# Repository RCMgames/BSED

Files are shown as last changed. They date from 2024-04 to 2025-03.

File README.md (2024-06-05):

# Byte Sized Encoder Decoder






Reads 8 quadrature encoders and communicates over I2C.

https://github.com/RCMgames/BSED

* Reads 8 quadrature encoders
* 1.0x0.85 inches, 25.4x21.59 millimeters
* I2C (Qwiic Compatible)
* powered by an ATmega328PB
* hand solderable surface mount components

### links 
(this repository contains an Arduino library, firmware for the board, and hardware for the board)
* [Documentation for Library](https://rcmgames.github.io/BSED/class_byte_sized_encoder_decoder.html)
* [Hardware](https://github.com/RCMgames/BSED/tree/main/extras/hardware)
  * If you buy PCBs from PCBWay through this link PCBWay generously gives me a 10% commission without costing you anything
    * https://www.pcbway.com/project/shareproject/ByteSizedEncoderDecoder_v1_1_a5a4bd50.html
* [Firmware](https://github.com/RCMgames/BSED/tree/main/extras/firmware)

### testing
Approximately 15000 encoder counts per second can be read from each encoder, but do your own testing before trusting this software.

See, and contribute to, this discussion on testing results: https://github.com/RCMgames/BSED/discussions/6

I've been working on [hardware and software for small wifi controlled robots](https://github.com/rcmgames) since 2020.

As I have designed increasingly small [circuit boards](https://github.com/rcmgames) for controlling servos and motors on robots, I started looking for a way to connect lots of quadrature encoders as inputs to a microcontroller. I was unable to find any existing Qwiic-compatible encoder reading boards that can handle multiple high-speed quadrature inputs. This board can help you control 8 motors with encoder feedback for precise control.

This version of firmware and library are compatible with version 1 of the hardware.

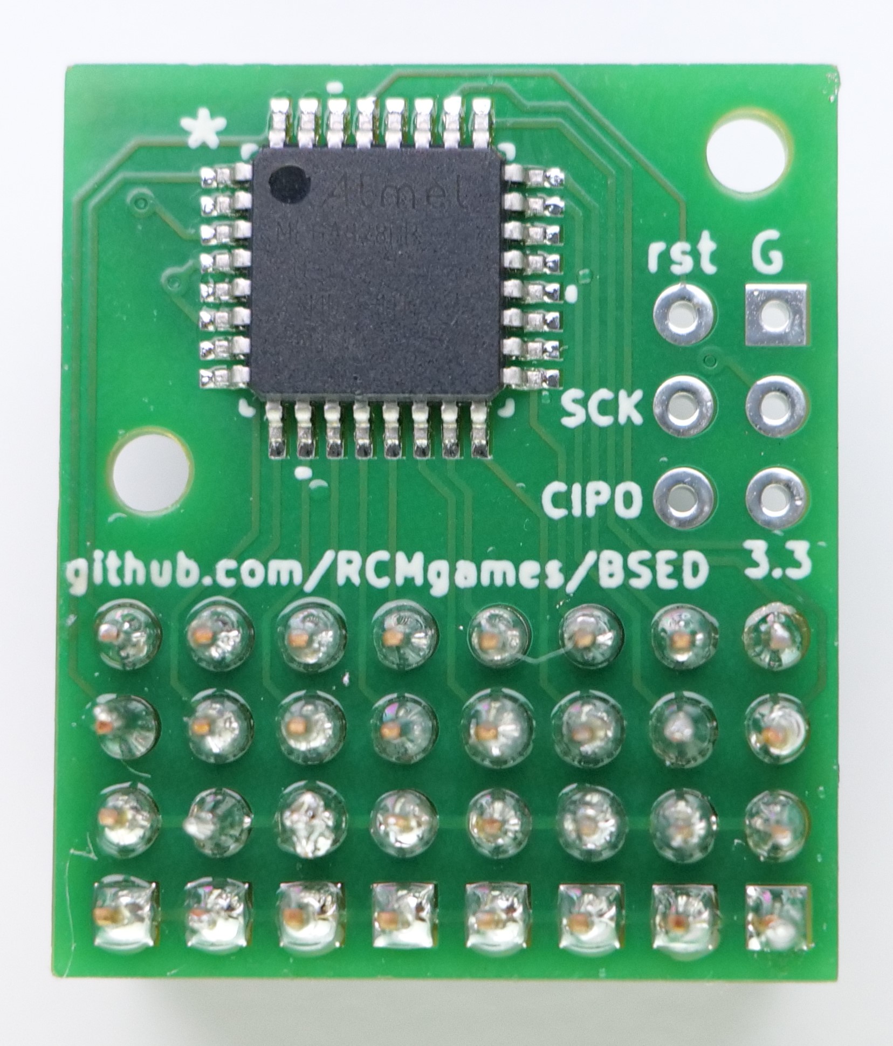
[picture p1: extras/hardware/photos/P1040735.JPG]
back of pcb

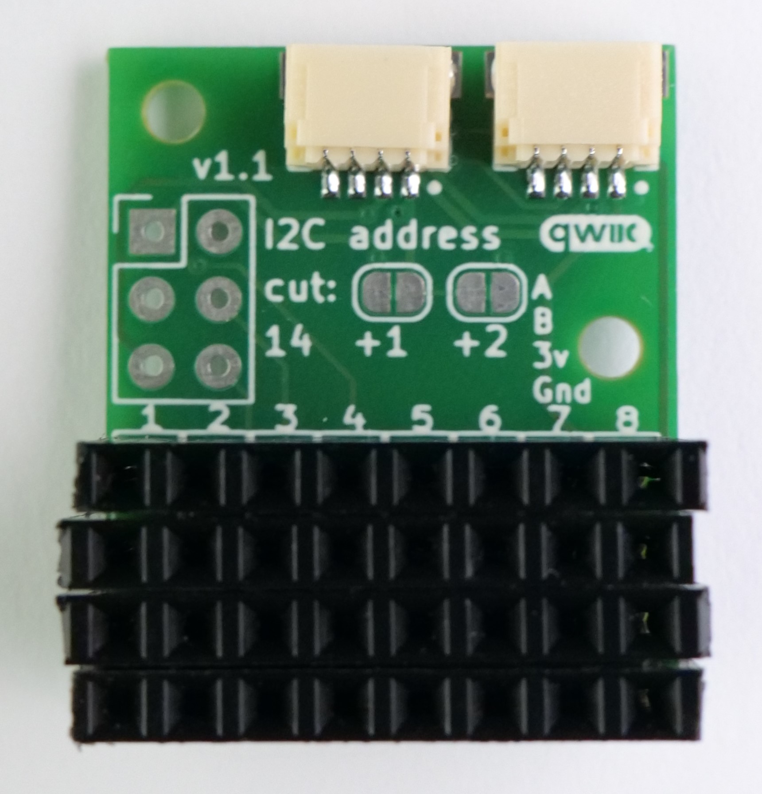
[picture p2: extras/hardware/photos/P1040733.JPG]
front of assembled pcb


## Acknowledgements
* I would like to thank [PCBWay](https://www.pcbway.com/) for sponsoring prototyping runs of this project. PCBWay produces very nice boards, supports open source hardware, and gave me great support as I worked on this project. Special thanks to Liam!

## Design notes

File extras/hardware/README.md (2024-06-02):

Here are the KiCAD and Gerber files for creating the circuit boards this firmware is designed to run on.

You could theoretically run it on a bare ATmega328 chip or another board, but the code is specialized for this board and uses hard-coded pin numbers.

### Bill Of Materials

* 1x assembled PCB
   * buy assembled PCBs from PCBWay with all the surface mount soldering done for you
      * https://www.pcbway.com/project/shareproject/ByteSizedEncoderDecoder_v1_1_a5a4bd50.html
   * or do your own surface mount soldering:
      * circuit board:
         * If you buy PCBs from PCBWay through this link PCBWay generously gives me a 10% commission without costing you anything
            * https://www.pcbway.com/project/shareproject/ByteSizedEncoderDecoder_v1_1_a5a4bd50.html
            * If you buy PCBs with another method (send ./PCB Production/gerbers-ByteSizedEncoderDecoder-v1.1.zip file) here's some info you might need: min track/spacing=6/6mil, min hole size=0.3mm
      * 2x JST SH https://www.digikey.com/en/products/detail/jst-sales-america-inc/SM04B-SRSS-TB/926710
      * 1x ATmega328PB TQFP https://www.digikey.com/en/products/detail/microchip-technology/ATMEGA328PB-AU/5638812
* 4x 1x08 0.1" female header pins

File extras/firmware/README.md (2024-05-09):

Use VSCode and PlatformIO to upload this (through ICSP) to the ATmega328P on the encoder reading board.

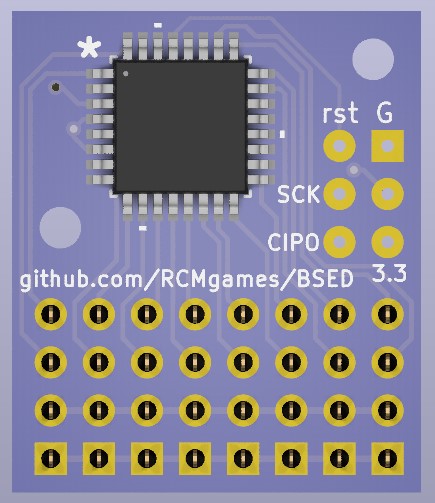
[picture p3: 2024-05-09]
extras/hardware/CAD renders/back.jpg

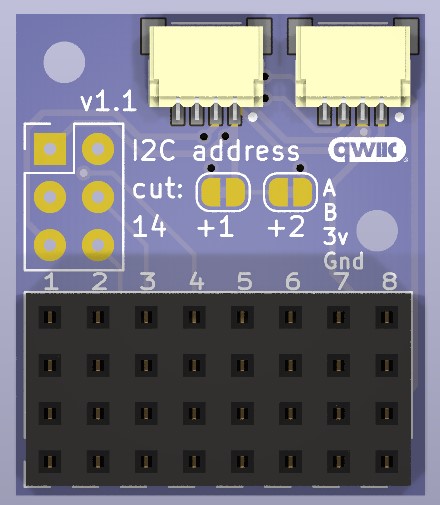
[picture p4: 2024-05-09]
extras/hardware/CAD renders/front.jpg

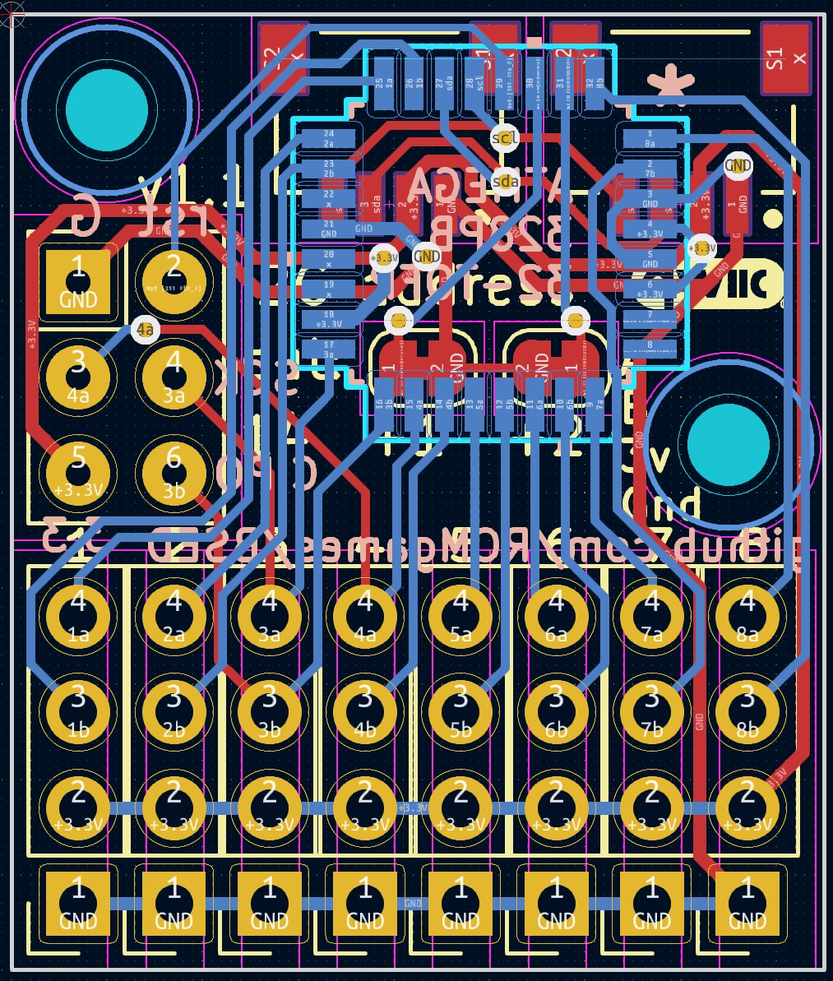
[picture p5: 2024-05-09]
extras/hardware/CAD renders/kicad.jpg

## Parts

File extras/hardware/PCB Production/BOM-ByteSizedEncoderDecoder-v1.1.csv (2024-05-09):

Reference | Value | Footprint | Datasheet | MPN | digikey link | Qty
J1, J2 | SM04B-SRSS-TB | parts:JST_SM04B-SRSS-TB_LF__SN_ |  | SM04B-SRSS-TB | 455-SM04B-SRSS-TBCT-ND | 2
J3-J10 | 1x4 female header pins 0.1" | Connector_PinSocket_2.54mm:PinSocket_1x04_P2.54mm_Vertical |  | do not place or purchase for PCB assembly | do not place or purchase for PCB assembly | 8
J11 | ICSP pads (for interfacing with pogo pins) | Connector_PinHeader_2.54mm:PinHeader_2x03_P2.54mm_Vertical |  | DNP | n/a | 1
NT1, NT2 | NetTie_2 | Jumper:SolderJumper-2_P1.3mm_Bridged_RoundedPad1.0x1.5mm | n/a | DNP | n/a | 2
U1 | ATMEGA328PB, 32-TQFP | parts:TQFP32_32A_MCH | https://ww1.microchip.com/downloads/en/DeviceDoc/40001907A.pdf | ATMEGA328PB-AU | ATMEGA328PB-AU-ND | 1

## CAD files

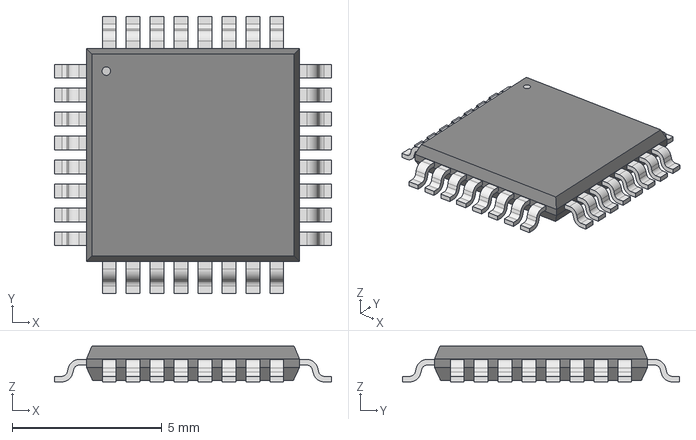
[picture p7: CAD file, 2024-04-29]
extras/hardware/parts/TQFP32_32A_MCH.step
9.25 x 9.25 x 1.20 mm

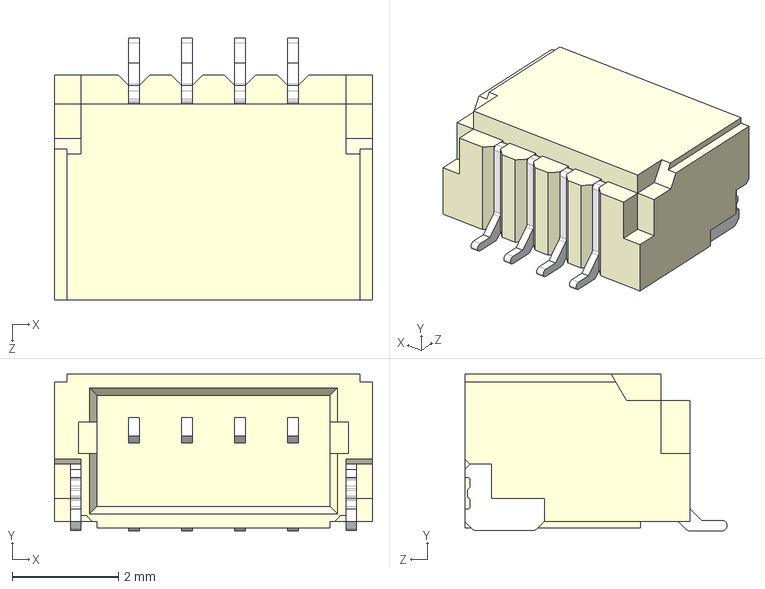
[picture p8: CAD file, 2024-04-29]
extras/hardware/parts/SM04B-SRSS-TB_LF__SN_.step
6.00 x 2.96 x 4.95 mm

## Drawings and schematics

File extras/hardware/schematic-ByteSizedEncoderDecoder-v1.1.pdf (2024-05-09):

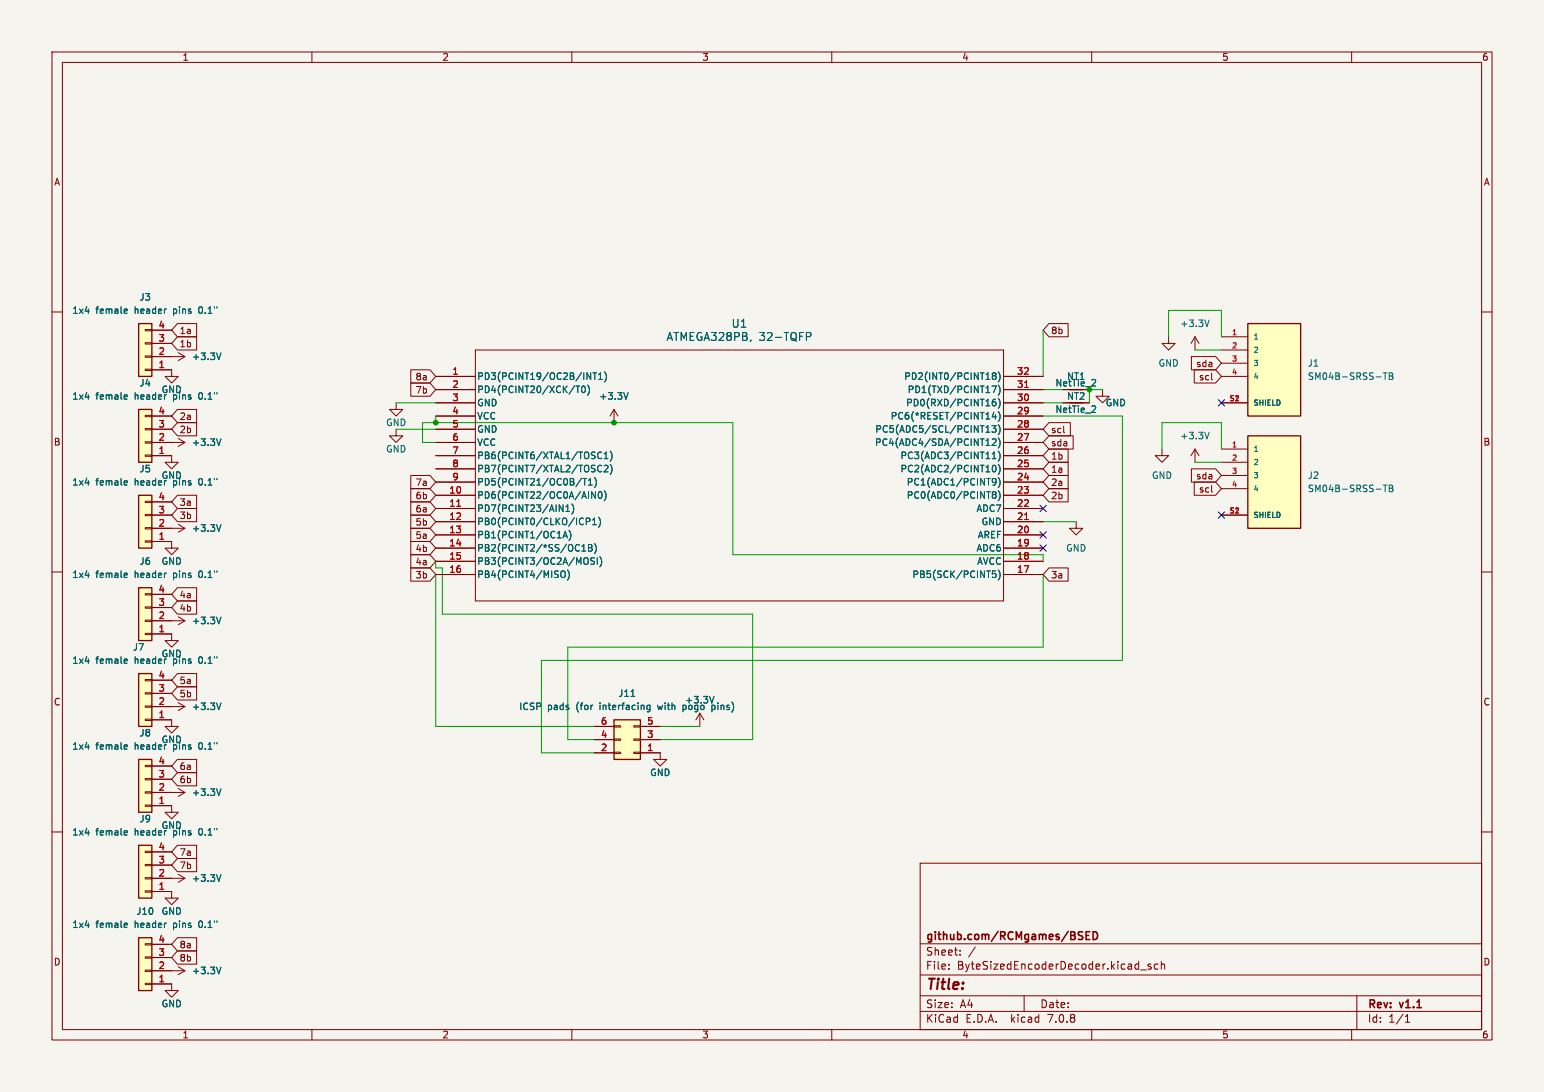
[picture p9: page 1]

1x4 female header pins 0.1" GND

1x4 female header pins 0.1" 1

1x4 female header pins 0.1" GND GND

Id: 1/1 Title: File: ByteSizedEncoderDecoder.kicad_sch Sheet: / github.com/RCMgames/BSED

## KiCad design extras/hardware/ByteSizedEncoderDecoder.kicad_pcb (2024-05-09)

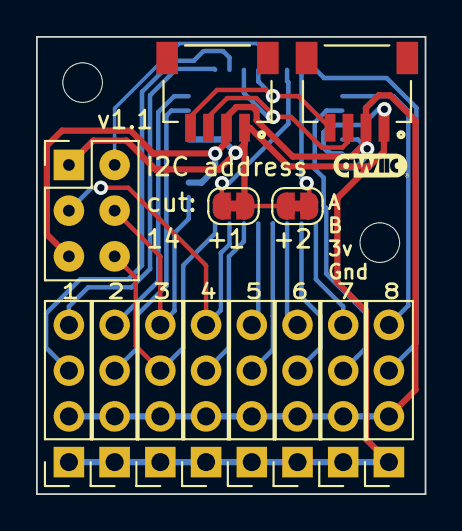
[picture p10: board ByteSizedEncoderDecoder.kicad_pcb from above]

Board: 2 copper layers, 21.6 x 25.4 mm, 14 parts (1 on the bottom side), 23 nets.

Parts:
J1, J2: SM04B-SRSS-TB; JST_SM04B-SRSS-TB_LF__SN_
J3, J4, J5, J6, J7, J8, J9, J10: 1x4 female header pins 0.1"; PinSocket_1x04_P2.54mm_Vertical
J11: ICSP pads (for interfacing with pogo pins); PinHeader_2x03_P2.54mm_Vertical
NT1, NT2: NetTie_2; SolderJumper-2_P1.3mm_Bridged_RoundedPad1.0x1.5mm
U1: ATMEGA328PB, 32-TQFP; TQFP32_32A_MCH

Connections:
1a: J3.4, U1.25 (PC2(ADC2/PCINT10))
1b: J3.3, U1.26 (PC3(ADC3/PCINT11))
2a: J4.4, U1.24 (PC1(ADC1/PCINT9))
2b: J4.3, U1.23 (PC0(ADC0/PCINT8))
3a: J5.4, J11.4, U1.17 (PB5(SCK/PCINT5))
3b: J5.3, J11.6, U1.16 (PB4(PCINT4/MISO))
4a: J6.4, J11.3, U1.15 (PB3(PCINT3/OC2A/MOSI))
4b: J6.3, U1.14 (PB2(PCINT2/*SS/OC1B))
5a: J7.4, U1.13 (PB1(PCINT1/OC1A))
5b: J7.3, U1.12 (PB0(PCINT0/CLKO/ICP1))
6a: J8.4, U1.11 (PD7(PCINT23/AIN1))
6b: J8.3, U1.10 (PD6(PCINT22/OC0A/AIN0))
7a: J9.4, U1.9 (PD5(PCINT21/OC0B/T1))
7b: J9.3, U1.2 (PD4(PCINT20/XCK/T0))
8a: J10.4, U1.1 (PD3(PCINT19/OC2B/INT1))
8b: J10.3, U1.32 (PD2(INT0/PCINT18))
+3.3V: J1.2, J2.2, J3.2, J4.2, J5.2, J6.2, J7.2, J8.2, J9.2, J10.2, J11.5, U1.4 (VCC), U1.6 (VCC), U1.18 (AVCC)
GND: J1.1, J2.1, J3.1, J4.1, J5.1, J6.1, J7.1, J8.1, J9.1, J10.1, J11.1, NT1.2, NT2.2, U1.3 (GND), U1.5 (GND), U1.21 (GND)
unnamed: J11.2, U1.29 (PC6(*RESET/PCINT14))
unnamed: NT2.1, U1.30 (PD0(RXD/PCINT16))
unnamed: NT1.1, U1.31 (PD1(TXD/PCINT17))
scl: J1.4, J2.4, U1.28 (PC5(ADC5/SCL/PCINT13))
sda: J1.3, J2.3, U1.27 (PC4(ADC4/SDA/PCINT12))

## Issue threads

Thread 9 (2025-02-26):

on an Arduino Uno, getPosition increments at a very fast rate but getPositionWithoutOverflows is fine.

joshua-8, 2025-02-26:
Velocity works fine.

I'll look into this.

joshua-8, 2025-03-20:
fixed in v2.2.5

(1<<15) was being interpreted as an int16_t on an Uno

Closed 2025-03-20.

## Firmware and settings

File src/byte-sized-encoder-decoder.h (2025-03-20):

#ifndef BYTE_SIZED_ENCODER_DECODER_H
#define BYTE_SIZED_ENCODER_DECODER_H
#include <Arduino.h>
#include <Wire.h>
/**
 * @brief class for communicating with the firmware on a Byte Sized Encoder Decoder board
 */
class ByteSizedEncoderDecoder {
protected:
    /**
     * @brief  I2C address of the Byte Sized Encoder Decoder board (as selected by the jumpers)
     */
    uint8_t address;
    /**
     * @brief  array of 8 numbers representing the number of steps each encoder has taken
     */
    int16_t encoderCount[8];
    /**
     * @brief  array of 8 numbers representing the number of times each encoder's counter variable has overflowed
     */
    int16_t encoderOverflows[8];
    /**
     * @brief  array of 8 numbers representing the last encoder count read from the board
     */
    int16_t lastEncoderCount[8];
    /**
     * @brief  array of 8 numbers representing the last encoder count read from the board for velocity calculation
     */
    int16_t lastVelocityEncoderCount[8];
    /**
     * @brief  I2C bus to communicate over.
     */
    TwoWire* wire;
    /**
     * @brief  bit mask of which encoders to read from
     */
    uint8_t whichEncodersMask;
    /**
     * @brief  the last time the encoders were read (microseconds)
     */
    unsigned long lastReadMicros[8];
    /**
     * @brief  array of 8 numbers representing the velocity of each encoder (steps per second)
     */
    int16_t encoderVelocity[8];
    /**
     * @brief  after this many milliseconds without an encoder tick velocity is set to zero.
     */
    int16_t encoderSlowestInterval[8];
    /**
     * @brief  enough counts to calculate velocity from
     */
    int16_t encoderEnoughCounts[8];
    /**
     * @brief  array of 8 booleans representing whether the velocity was just calculated
     */
    boolean isVelNewVal[8];
    /**
     * @brief  helper function to write a byte to the board
     */
    inline void write(uint8_t data)
    {
        wire->beginTransmission(address);
        wire->write(data);
        wire->endTransmission();
    }

public:
    /**
     * @brief Constructor for the Byte Sized Encoder Decoder class
     * @param  _wire: I2C bus to communicate over. &Wire or &Wire1
     * @param  _address: I2C address of the Byte Sized Encoder Decoder board (as selected by the jumpers), default is 14, (14-17 are options)
     * @param  _encoderSlowestInterval: after this many milliseconds without a calculation, velocity is recalculated
     * @param  _encoderEnoughCounts: enough counts to calculate velocity
     */
    ByteSizedEncoderDecoder(TwoWire* _wire, uint8_t _address = 14, int16_t _encoderSlowestInterval = 0, int16_t _encoderEnoughCounts = 0)
    {
        wire = _wire;
        address = _address;
        whichEncodersMask = 255;

        // memset encoderCount[] all 0
        memset(encoderCount, 0, 8 * sizeof(int16_t));
        memset(encoderOverflows, 0, 8 * sizeof(int16_t));
        memset(lastEncoderCount, 0, 8 * sizeof(int16_t));
        memset(lastVelocityEncoderCount, 0, 8 * sizeof(int16_t));
        memset(lastReadMicros, 0, 8 * sizeof(unsigned long));
        memset(encoderVelocity, 0, 8 * sizeof(int16_t));
        memset(encoderSlowestInterval, _encoderSlowestInterval, 8 * sizeof(int16_t));
        memset(encoderEnoughCounts, _encoderEnoughCounts, 8 * sizeof(int16_t));
        memset(isVelNewVal, 0, 8 * sizeof(boolean));
    }
    /**
     * @brief set the value of encoderSlowestInterval
     * @param  n: encoder number (1-8), or 0 to set all at once
     * @param  interval: after this many milliseconds without a calculation, velocity is recalculated
     */
    void setEncoderSlowestInterval(uint8_t n, int16_t interval)
    {
        if (n > 8) {
            return;
        }
        if (n == 0) {
            for (byte i = 0; i < 8; i++) {
                encoderSlowestInterval[i] = interval;
            }
            return;
        }
        encoderSlowestInterval[n - 1] = interval;
    }
    /**
     * @brief set the value of encoderEnoughCounts
     * @param  n: encoder number (1-8), or 0 to set all at once
     * @param  counts: enough counts to calculate velocity
     */
    void setEncoderEnoughCounts(uint8_t n, int16_t counts)
    {
        if (n > 8) {
            return;
        }
        if (n == 0) {
            for (byte i = 0; i < 8; i++) {
                encoderEnoughCounts[i] = counts;
            }
            return;
        }
        encoderEnoughCounts[n - 1] = counts;
    }

    /**
     * @brief  whether the velocity was just calculated
     * @note this function resets the value to false, so call it just once
     * @param  n: encoder number (1-8)
     * @retval boolean: whether the velocity was just calculated
     */
    boolean isVelNew(uint8_t n)
    {
        if (n > 8 || n < 1) {
            return false;
        }
        boolean temp = isVelNewVal[n - 1];
        isVelNewVal[n - 1] = false;
        return temp;
    }
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

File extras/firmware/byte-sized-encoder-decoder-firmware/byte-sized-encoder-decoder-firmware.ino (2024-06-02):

#include <Arduino.h>
const uint8_t PORTB_used_pins_mask = 0b00111111; // D13-D8
volatile uint8_t lastPortBPinStates = PORTB_used_pins_mask;
const uint8_t PORTC_used_pins_mask = 0b00001111; // A3-A0
volatile uint8_t lastPortCPinStates = PORTC_used_pins_mask;
const uint8_t PORTD_used_pins_mask = 0b11111100; // D7-D2
volatile uint8_t lastPortDPinStates = PORTD_used_pins_mask;

volatile uint16_t encoderCount[8] = { 0, 0, 0, 0, 0, 0, 0, 0 };

volatile uint8_t requestNumber = 255;

volatile uint8_t dataToSend[17] = { 0, 0, 0, 0, 0, 0, 0, 0, 0, 0, 0, 0, 0, 0, 0, 0, 0 };

volatile int16_t onReceiveData = 0;

void setup()
{
    pinMode(0, INPUT_PULLUP); // for address
    pinMode(1, INPUT_PULLUP); // for address

    pinMode(2, INPUT_PULLUP); // encoder pins are INPUT_PULLUP to prevent unused pins from floating
    pinMode(3, INPUT_PULLUP);
    pinMode(4, INPUT_PULLUP);
    pinMode(5, INPUT_PULLUP);
    pinMode(6, INPUT_PULLUP);
    pinMode(7, INPUT_PULLUP);
    pinMode(8, INPUT_PULLUP);
    pinMode(9, INPUT_PULLUP);
    pinMode(10, INPUT_PULLUP);
    pinMode(11, INPUT_PULLUP);
    pinMode(12, INPUT_PULLUP);
    pinMode(13, INPUT_PULLUP);
    pinMode(A0, INPUT_PULLUP);
    pinMode(A1, INPUT_PULLUP);
    pinMode(A2, INPUT_PULLUP);
    pinMode(A3, INPUT_PULLUP);
    delay(1);

    cli();
    PCICR |= 0b00000111; // turn on all pin change interrupts
    PCMSK0 = PORTB_used_pins_mask;
    PCMSK1 = PORTC_used_pins_mask;
    PCMSK2 = PORTD_used_pins_mask;

    twi_init(14 + digitalRead(0) + 2 * digitalRead(1)); // 14,15,16,17

    sei();
}

void loop()
{
}

// lots of I2C code from https://github.com/arduino/ArduinoCore-avr/blob/321fca0bac806bdd36af8afbc13587f4b67eb5f1/libraries/Wire/src/utility/twi.c (but modified)

#define cbi(sfr, bit) (_SFR_BYTE(sfr) &= ~_BV(bit))
#define TW_ST_SLA_ACK 0xA8
#define TW_ST_ARB_LOST_SLA_ACK 0xB0
#define TW_ST_DATA_ACK 0xB8
#define TW_ST_DATA_NACK 0xC0
#define TW_ST_LAST_DATA 0xC8
#define TW_SR_SLA_ACK 0x60
#define TW_SR_ARB_LOST_SLA_ACK 0x68
#define TW_SR_GCALL_ACK 0x70
#define TW_SR_ARB_LOST_GCALL_ACK 0x78
#define TW_SR_DATA_ACK 0x80
#define TW_SR_DATA_NACK 0x88
#define TW_SR_GCALL_DATA_ACK 0x90
#define TW_SR_GCALL_DATA_NACK 0x98
#define TW_SR_STOP 0xA0
#define TW_NO_INFO 0xF8
#define TW_BUS_ERROR 0x00
#define TW_STATUS_MASK (_BV(TWS7) | _BV(TWS6) | _BV(TWS5) | _BV(TWS4) | _BV(TWS3))
#define TW_STATUS (TWSR & TW_STATUS_MASK)
#define TW_READ 1
#define TW_WRITE 0

#define TWI_READY 0
#define TWI_SRX 3
#define TWI_STX 4
#define TWI_BUFFER_SIZE 17

volatile uint8_t twi_state;
static volatile uint8_t twi_txBufferIndex;
static volatile uint8_t twi_txBufferLength;
static uint8_t twi_rxBuffer[TWI_BUFFER_SIZE];
static volatile uint8_t twi_rxBufferIndex;
volatile uint8_t twi_error;

void twi_init(uint8_t address)
{
    twi_state = TWI_READY;
    // activate internal pullups for twi.
    digitalWrite(SDA, 1);
    digitalWrite(SCL, 1);

    TWAR = address << 1; // set twi peripheral address (skip over TWGCE bit)

    TWCR = _BV(TWEN) | _BV(TWIE) | _BV(TWEA);
}
void twi_releaseBus(void)
{
    // release bus
    TWCR = _BV(TWEN) | _BV(TWIE) | _BV(TWEA) | _BV(TWINT);

    // update twi state
    twi_state = TWI_READY;
}

inline void twi_reply(uint8_t ack)
{
    // transmit controller read ready signal, with or without ack
    if (ack) {
        TWCR = _BV(TWEN) | _BV(TWIE) | _BV(TWINT) | _BV(TWEA);
    } else {
        TWCR = _BV(TWEN) | _BV(TWIE) | _BV(TWINT);
    }
}

/*
 * Function twi_stop
 * Desc     relinquishes bus controller status
 * Input    none
 * Output   none
 */
void twi_stop(void)
{
    // send stop condition
    TWCR = _BV(TWEN) | _BV(TWIE) | _BV(TWEA) | _BV(TWINT) | _BV(TWSTO);
    while (TWCR & _BV(TWSTO)) {
        continue;
    }
    // update twi state
    twi_state = TWI_READY;
}

inline void onReceive(uint8_t* dataBuf, int nData)
{
    onReceiveData = dataBuf[0];
    if (onReceiveData == 0) {
        encoderCount[0] = 0;
        encoderCount[1] = 0;
        encoderCount[2] = 0;
        encoderCount[3] = 0;
        encoderCount[4] = 0;
        encoderCount[5] = 0;
        encoderCount[6] = 0;
        encoderCount[7] = 0;
    } else if (onReceiveData > 0 && onReceiveData <= 0xFF) {
        requestNumber = onReceiveData;
        twi_txBufferLength = 0;
        twi_txBufferIndex = 0;
        if (bitRead(requestNumber, 7)) {
            dataToSend[twi_txBufferLength] = highByte(encoderCount[0]);
            twi_txBufferLength++;
            dataToSend[twi_txBufferLength] = lowByte(encoderCount[0]);
            twi_txBufferLength++;
        }
        if (bitRead(requestNumber, 6)) {
            dataToSend[twi_txBufferLength] = highByte(encoderCount[1]);
            twi_txBufferLength++;
            dataToSend[twi_txBufferLength] = lowByte(encoderCount[1]);
            twi_txBufferLength++;
        }
        if (bitRead(requestNumber, 5)) {
            dataToSend[twi_txBufferLength] = highByte(encoderCount[2]);
            twi_txBufferLength++;
            dataToSend[twi_txBufferLength] = lowByte(encoderCount[2]);
            twi_txBufferLength++;
        }
        if (bitRead(requestNumber, 4)) {
            dataToSend[twi_txBufferLength] = highByte(encoderCount[3]);
            twi_txBufferLength++;
            dataToSend[twi_txBufferLength] = lowByte(encoderCount[3]);
            twi_txBufferLength++;
        }
        if (bitRead(requestNumber, 3)) {
            dataToSend[twi_txBufferLength] = highByte(encoderCount[4]);
            twi_txBufferLength++;
            dataToSend[twi_txBufferLength] = lowByte(encoderCount[4]);
            twi_txBufferLength++;
        }
        if (bitRead(requestNumber, 2)) {
            dataToSend[twi_txBufferLength] = highByte(encoderCount[5]);
            twi_txBufferLength++;
            dataToSend[twi_txBufferLength] = lowByte(encoderCount[5]);
            twi_txBufferLength++;
        }
        if (bitRead(requestNumber, 1)) {
            dataToSend[twi_txBufferLength] = highByte(encoderCount[6]);
            twi_txBufferLength++;
            dataToSend[twi_txBufferLength] = lowByte(encoderCount[6]);
            twi_txBufferLength++;
        }
        if (bitRead(requestNumber, 0)) {
            dataToSend[twi_txBufferLength] = highByte(encoderCount[7]);
            twi_txBufferLength++;
            dataToSend[twi_txBufferLength] = lowByte(encoderCount[7]);
            twi_txBufferLength++;
        }
    }
}

ISR(TWI_vect)
{
    switch (TW_STATUS) {
        // peripheral Receiver
    case TW_SR_SLA_ACK: // addressed, returned ack
    case TW_SR_GCALL_ACK: // addressed generally, returned ack
    case TW_SR_ARB_LOST_SLA_ACK: // lost arbitration, returned ack
    case TW_SR_ARB_LOST_GCALL_ACK: // lost arbitration, returned ack
        // enter peripheral receiver mode
        twi_state = TWI_SRX;
        // indicate that rx buffer can be overwritten and ack
        twi_rxBufferIndex = 0;
        twi_reply(1);
        break;
    case TW_SR_DATA_ACK: // data received, returned ack
    case TW_SR_GCALL_DATA_ACK: // data received generally, returned ack
        // if there is still room in the rx buffer
        if (twi_rxBufferIndex < TWI_BUFFER_SIZE) {
            // put byte in buffer and ack
            twi_rxBuffer[twi_rxBufferIndex++] = TWDR;
            twi_reply(1);
        } else {
            // otherwise nack
            twi_reply(0);
        }
        break;
    case TW_SR_STOP: // stop or repeated start condition received
        // ack future responses and leave peripheral receiver state
        twi_releaseBus();
        // put a null char after data if there's room
        if (twi_rxBufferIndex < TWI_BUFFER_SIZE) {
            twi_rxBuffer[twi_rxBufferIndex] = '\0';
        }
        // callback to user defined callback
        onReceive(twi_rxBuffer, twi_rxBufferIndex);
        // since we submit rx buffer to "wire" library, we can reset it
        twi_rxBufferIndex = 0;
        break;
    case TW_SR_DATA_NACK: // data received, returned nack
    case TW_SR_GCALL_DATA_NACK: // data received generally, returned nack
        // nack back at controller
        twi_reply(0);
        break;

    // peripheral Transmitter
    case TW_ST_SLA_ACK: // addressed, returned ack
    case TW_ST_ARB_LOST_SLA_ACK: // arbitration lost, returned ack
        // enter peripheral transmitter mode
        twi_state = TWI_STX;
        // ready the tx buffer index for iteration
        // set tx buffer length to be zero, to verify if user changes it
        // request for txBuffer to be filled and length to be set
        // note: user must call twi_transmit(bytes, length) to do this
        // onRequest();
        // transmit first byte from buffer, fall
        /* fall through */
    case TW_ST_DATA_ACK: // byte sent, ack returned
        // copy data to output register
        TWDR = dataToSend[twi_txBufferIndex++];
        // if there is more to send, ack, otherwise nack
        if (twi_txBufferIndex >= 17) { // don't overflow dataToSend (there's an extra byte at the end)
            twi_txBufferIndex = 16;
        }
        twi_reply(0); // send bytes one at a time
        break;
    case TW_ST_DATA_NACK: // received nack, we are done
    case TW_ST_LAST_DATA: // received ack, but we are done already!
        // ack future responses
        twi_reply(1);
        // leave peripheral receiver state
        twi_state = TWI_READY;
        break;

    // All
    case TW_NO_INFO: // no state information
        break;
    case TW_BUS_ERROR: // bus error, illegal stop/start
        twi_error = TW_BUS_ERROR;
        twi_stop();
        break;
    }
}

ISR(PCINT0_vect)
{
    // D13-D8
    uint8_t pinStates = PINB & PORTB_used_pins_mask;
    uint8_t changedPins = pinStates ^ lastPortBPinStates;
    lastPortBPinStates = pinStates;

    if (bitRead(changedPins, 0))
        (bitRead(pinStates, 0) == bitRead(pinStates, 1)) ? encoderCount[4]-- : encoderCount[4]++;
    if (bitRead(changedPins, 1))
        (bitRead(pinStates, 0) != bitRead(pinStates, 1)) ? encoderCount[4]-- : encoderCount[4]++;
    if (bitRead(changedPins, 2))
        (bitRead(pinStates, 2) == bitRead(pinStates, 3)) ? encoderCount[3]-- : encoderCount[3]++;
    if (bitRead(changedPins, 3))
        (bitRead(pinStates, 2) != bitRead(pinStates, 3)) ? encoderCount[3]-- : encoderCount[3]++;
    if (bitRead(changedPins, 4))
        (bitRead(pinStates, 4) == bitRead(pinStates, 5)) ? encoderCount[2]-- : encoderCount[2]++;
    if (bitRead(changedPins, 5))
        (bitRead(pinStates, 4) != bitRead(pinStates, 5)) ? encoderCount[2]-- : encoderCount[2]++;
}

ISR(PCINT1_vect)
{
    // A3-A0
    uint8_t pinStates = PINC & PORTC_used_pins_mask; // A3-A0
    uint8_t changedPins = pinStates ^ lastPortCPinStates;
    lastPortCPinStates = pinStates;
    if (bitRead(changedPins, 0))
        (bitRead(pinStates, 0) == bitRead(pinStates, 1)) ? encoderCount[1]-- : encoderCount[1]++;
    if (bitRead(changedPins, 1))
        (bitRead(pinStates, 0) != bitRead(pinStates, 1)) ? encoderCount[1]-- : encoderCount[1]++;
    if (bitRead(changedPins, 2))
        (bitRead(pinStates, 2) == bitRead(pinStates, 3)) ? encoderCount[0]++ : encoderCount[0]--;
    if (bitRead(changedPins, 3))
        (bitRead(pinStates, 2) != bitRead(pinStates, 3)) ? encoderCount[0]++ : encoderCount[0]--;
}
ISR(PCINT2_vect)
{
    uint8_t pinStates = PIND & PORTD_used_pins_mask; // D7-D2
    uint8_t changedPins = pinStates ^ lastPortDPinStates;
    lastPortDPinStates = pinStates;
    if (bitRead(changedPins, 2))
        (bitRead(pinStates, 2) == bitRead(pinStates, 3)) ? encoderCount[7]-- : encoderCount[7]++;
    if (bitRead(changedPins, 3))
        (bitRead(pinStates, 2) != bitRead(pinStates, 3)) ? encoderCount[7]-- : encoderCount[7]++;
    if (bitRead(changedPins, 4))
        (bitRead(pinStates, 4) == bitRead(pinStates, 5)) ? encoderCount[6]-- : encoderCount[6]++;
    if (bitRead(changedPins, 5))
        (bitRead(pinStates, 4) != bitRead(pinStates, 5)) ? encoderCount[6]-- : encoderCount[6]++;
    if (bitRead(changedPins, 6))
        (bitRead(pinStates, 6) == bitRead(pinStates, 7)) ? encoderCount[5]-- : encoderCount[5]++;
    if (bitRead(changedPins, 7))
        (bitRead(pinStates, 6) != bitRead(pinStates, 7)) ? encoderCount[5]-- : encoderCount[5]++;
}

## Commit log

2024-04-30 add cad renders
2024-04-30 update encoder-decoder
2024-04-30 reorganize folder structure
    [32M1-A_ATM.step, BM04B-SRSS-TB_LF__SN_.step, ByteSizedEncoderDecoder.kicad_pcb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]
2024-05-07 update arduino-lint
2024-05-08 test board
2024-05-08 fix link
    [ByteSizedEncoderDecoder.kicad_pcb, ByteSizedEncoderDecoder.kicad_sch]
2024-06-01 v2 (velocity calculation and optimized communication)
2024-06-02 reset velocity when resetting position
    [byte-sized-encoder-decoder.h]
2024-06-02 v2.3.3 bugfix for velocity calcs
    [byte-sized-encoder-decoder.h]
2024-06-04 fix bug in resetting variables
    [byte-sized-encoder-decoder.h]
